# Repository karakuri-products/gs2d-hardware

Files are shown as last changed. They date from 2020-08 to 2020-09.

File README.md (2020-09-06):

# gs2d-hardware (gs2d Hardware Manual)

> gs2d ライブラリ・ハードウェアマニュアル

---

## gs2d 対応製品

gs2d 対応が確認できているシリアルサーボ・ドライバは表 1 のとおりです。

> 表 1 　対応製品一覧

| Manufacturer | Product Name |
| --- | --- |
| karakuri products Inc. | kr-gs2d001 |

karakuri products 社の kr-gs2d001 については ./kr-gs2d001 にまとめています。

---

## ドライバを自作する場合

### ハードウェア要件

gs2d に対応するシリアルサーボ・ドライバを開発する際、以下を満たしてください。

> 1. シリアル信号の送信/受信ライン間のループバックは回路的に無視すること。[↓](#ループバック処理)
> 2. 入力するシリアルおよび GPIO の I/O レベルが 5V 以下の場合は適宜、レベル変換を実装すること。[↓](#レベル変換)

### 設計例

#### ループバック処理

gs2d 対応シリアルバスの設計例を図 1 に示します。

入力するシリアルに対する送信許可信号（TxDEN）を 3 ステートバッファの制御信号に接続します。これにより信号の流れを制御し、送信コマンドの受信側へのループバックを回路的に無視することができます。

<div align="center">
    gs2d-hw fig.1
</div>

> 図 1 ループバック処理の一例

gs2d でサポートするシリアルサーボのバスの物理層は RS485、1 wire TTL Serial の 2 種に大別できます。各規格でのループバック処理の設計例は図 2、図 3 を参照ください。

<div align="center">
    gs2d-hw fig.2
</div>

> 図 2 RS485 方式での設計例

<div align="center">
    gs2d-hw fig.3
</div>

> 図 3 1 wire TTL Serial 方式での設計例

##### TxDEN について

FT232 などの USB シリアルドライバを利用する際は提供される TxDEN をそのまま活用できます。例えば、FT232 では出荷設定では CBUS2 端子に TxDEN 出力が割り当てられており、これを接続します（図 4）。

<div align="center">
    gs2d-hw fig.4
</div>

> 図 4 FT232 での接続例

Arduino、Teensy 等のマイコンからシリアルを入力する場合、TxDEN に適当な GPIO を接続します。この GPIO をシリアル送信/受診時に適切に制御することで、コマンドのループバックを遮断します。Arduino UNO での例を図 5 に示します。

接続した GPIO の制御は gs2d-cpp ライブラリの How to Use を確認ください。

<div align="center">
    gs2d-hw fig.5
</div>

> 図 5 Arduino UNO での接続例<br>
> (この例では、ディジタルピン 2 を TxDEN として活用、シリアルはハードウェア・シリアル)

#### レベル変換

シリアルサーボ側の信号ラインは一般的に +5V レベルが採用されており、 gs2d もこれに準じます。

上記の例（図 4 ～ 5）では、入力する RX、TX、TXDEN の I/O レベルが +5V であると仮定し、直接、シリアルバス・ドライバに接続していました。しかしそうでない場合（5V 未満の場合）は双方向レベル変換回路を接続し、I/O レベルの差異を吸収してください。

双方向レベル変換回路の具体的な設計例を図 6 に示します。この設計例は V<sub>IOREF</sub> = +5V の場合も対応します。

<div align="center">
    gs2d-hw fig.6
</div>

> 図 6 Nch MOS-FET を用いた双方向レベル変換回路の一例<br>
> R は 10kΩ 程度の抵抗、Q は Nch MOS-FET。V<sub>IOREF</sub> には低電圧 Lv. I/O 側の基準電圧を接続します。

図 6 を組込んだシリアルバス・ドライバの設計例を図 7 に示します。

<div align="center">
    gs2d-hw fig.７
</div>

> 図 7 レベル変換を組込んだシリアルバスドライバ回路の一例<br>
> (入力信号側の I/O レベルが +3.3V の場合)

より詳細な設計例は gs2d に対応済みのシリアルサーボドライバ kr-gs2d001 (karakuri products 製) の<a href="./kr-gs2d001/kr-gs2d001_schematic.pdf">回路図</a>を参照ください。

---

## ライセンス

gs2d は Apache License 2.0 とします。詳細は ./LICENSE を参照のこと。

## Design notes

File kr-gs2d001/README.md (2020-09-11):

# kr-gs2d001

> gs2d 対応 シリアルサーボ・ドライバ kr-gs2d001

<div align="center">
    gs2d-hw fig.1
</div>

---

## 概要

kr-gs2d001 は、gs2d ライブラリに対応したシリアルサーボ・ドライバです。

本製品と gs2d ライブラリにより、 2 種類の規格 ( RS485、1 wire TTL Serial ) のシリアルサーボを PC およびマイコンから簡単に制御することができます。

<div align="center">
    gs2d-hw fig.1
</div>

> 図 1 kr-gs2d001 外観 (左: 正面、右: 背面)

<div align="center">
    gs2d-hw fig.1
</div>

> 図 2 kr-gs2d001 ブロック図

---

### 対応シリアルサーボ

kr-gs2d001 でサポートするメーカ/規格は表 2 のとおりです。対応/動作確認が完了しているシリアルサーボの機種は<a href="https://docs.google.com/spreadsheets/d/15XlF4kySq219ICrvgJmQ_NEENOpA3_AKKTeR7gI3orM/edit?usp=sharing" target="_blank">こちら</a>で確認できます。

> 表 1 サポートするメーカ/規格

| Manufacturer | Series | Protocol |
| --- | --- | --- |
| ロボティズ (ROBOTIS Inc.) | Dynamixel X Series | Protocol 2.0 |
| 近藤科学 (Kondo Kagaku Co.,Ltd.) | B3M Serises <br> KRS Series | B3M protocol <br> ICS3.6 <br> ICS3.5 |
| 双葉電子工業 (FUTABA Corp.) | Command Type Servo | Command Type Protocol |

---

### 機械的仕様

> 表 2 機械的仕様

| 項目 | 仕様 |
| --- | --- |
| 基板外形 | 54.0 mm x 74.0 mm |

#### 3D モデルデータ

<a href="./3dmodel"> ./3dmodel </a>にて提供します。形式は表 3 のとおり。

> 表 3 提供モデルデータ形式一覧

| 拡張子 | 形式名 | 備考 |
| --- | --- | --- |
| .f3d | Autodesk FUSIN360 形式 | |
| .iam / .ipt | Autodesk Inventor 形式 | zip 形式で圧縮 |
| .iges | IGES 形式 | |
| .sat | SAT 形式 | |
| .step | IGES 形式 | |

#### コネクタ配置

> 表 4 コネクタ一覧

| 番号 | 種類 | 用途 |
| --- | --- | --- |
| CN1 ~ CN4 | JST-XH 4p | KONDO B3M (RS485) |
| CN5 ~ CN8 | JST-EH 4p | ROBOTIS Dynamixel X (RS485) |
| CN9 ~ CN12  | JST-EH 4p | FUTABA RS40x (RS485) |
| CN13 ~ CN16 | JST-ZH 3p | KONDO KRS33xx (1 wire TTL)  |
| CN17 ~ CN20 | QI(2550) 3p | 1 wire TTL Serial 共用 |
| CN21 ~ CN24 | JST-ADH 3p | FUTABA RS20x (1 wire TTL) |
| CN25 ~ CN28 | QI(2550) 6p,8p x2,10p | Arduino シールド |
| CN29 | USB typeC | USB2.1, PD 非対応 |
| CN30 | AMASS-XT60 2p | 電源コネクタ |

#### 部品配置

> 表 5 主要部品一覧

| 番号 | 用途 |
| --- | --- |
| SW1 | RS485 / 1 wire TTL Serial 切替え (図 3) |
| SW2 | USB シリアル入力 (USB typeC 経由) / Arduino シリアル入力 (もしくは外部シリアル入力) 切替え (図 4) |
| LED1 | USB シリアル TxLED |
| LED2 | USB シリアル RxLED |
| LED3 | 電源 LED |
| SJ1/SJ2 | Arduino ハードウェア/ソフトウェア シリアル切替え (図 5) |

<div align="center">
    sw1 fig.2
</div>

> 図 3 SW1 によるシリアル信号の通信規格の切替え<br>
> (a) RS485, (b) 1 wire TTL Serial

<div align="center">
    sw1 fig.3
</div>

> 図 4 SW2 による入力シリアル信号の切替え<br>
> (a) USB シリアル入力 (USB typeC 経由), (b) Arduino シリアル入力 (もしくは外部シリアル入力)

<div align="center">
    GettingStarted fig.1
</div>

> 図 5 Arduino ハードウェア/ソフトウェア シリアル切替え(SJ1/SJ2)

---

### 電気的仕様

> 表 6 電気的仕様一覧

| パラメータ | 値 |
| --- | --- |
| 電源電圧 | 5.0 ～ 24.0V |
| 対応入力 I/O レベル | 3.0 ～ 5.0V  |

#### 回路図

<a href="./kr-gs2d001_schematic.pdf"> kr-gs2d001_schematic.pdf </a> に示します。

---

## ライセンス

kr-gs2d001 は Apache License 2.0 とします。詳細は LICENSE 参照。

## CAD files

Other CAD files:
kr-gs2d001/3dmodel/kr-gs2d001.f3d

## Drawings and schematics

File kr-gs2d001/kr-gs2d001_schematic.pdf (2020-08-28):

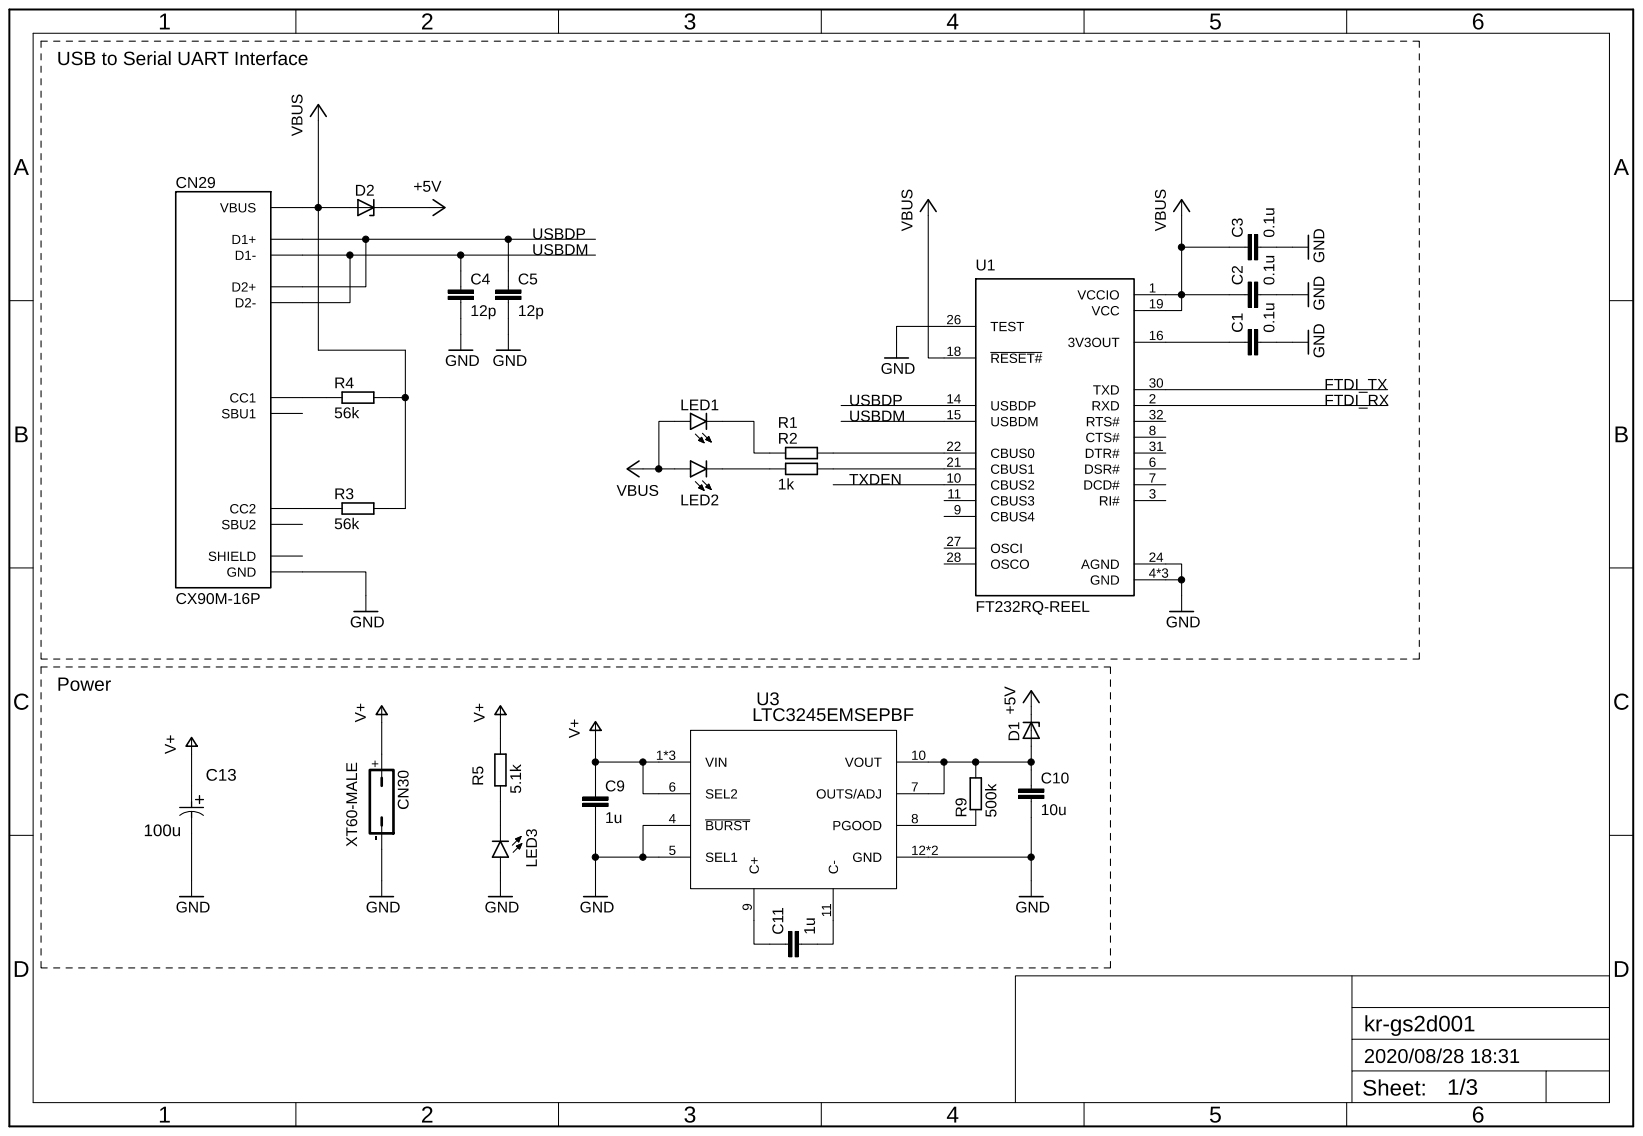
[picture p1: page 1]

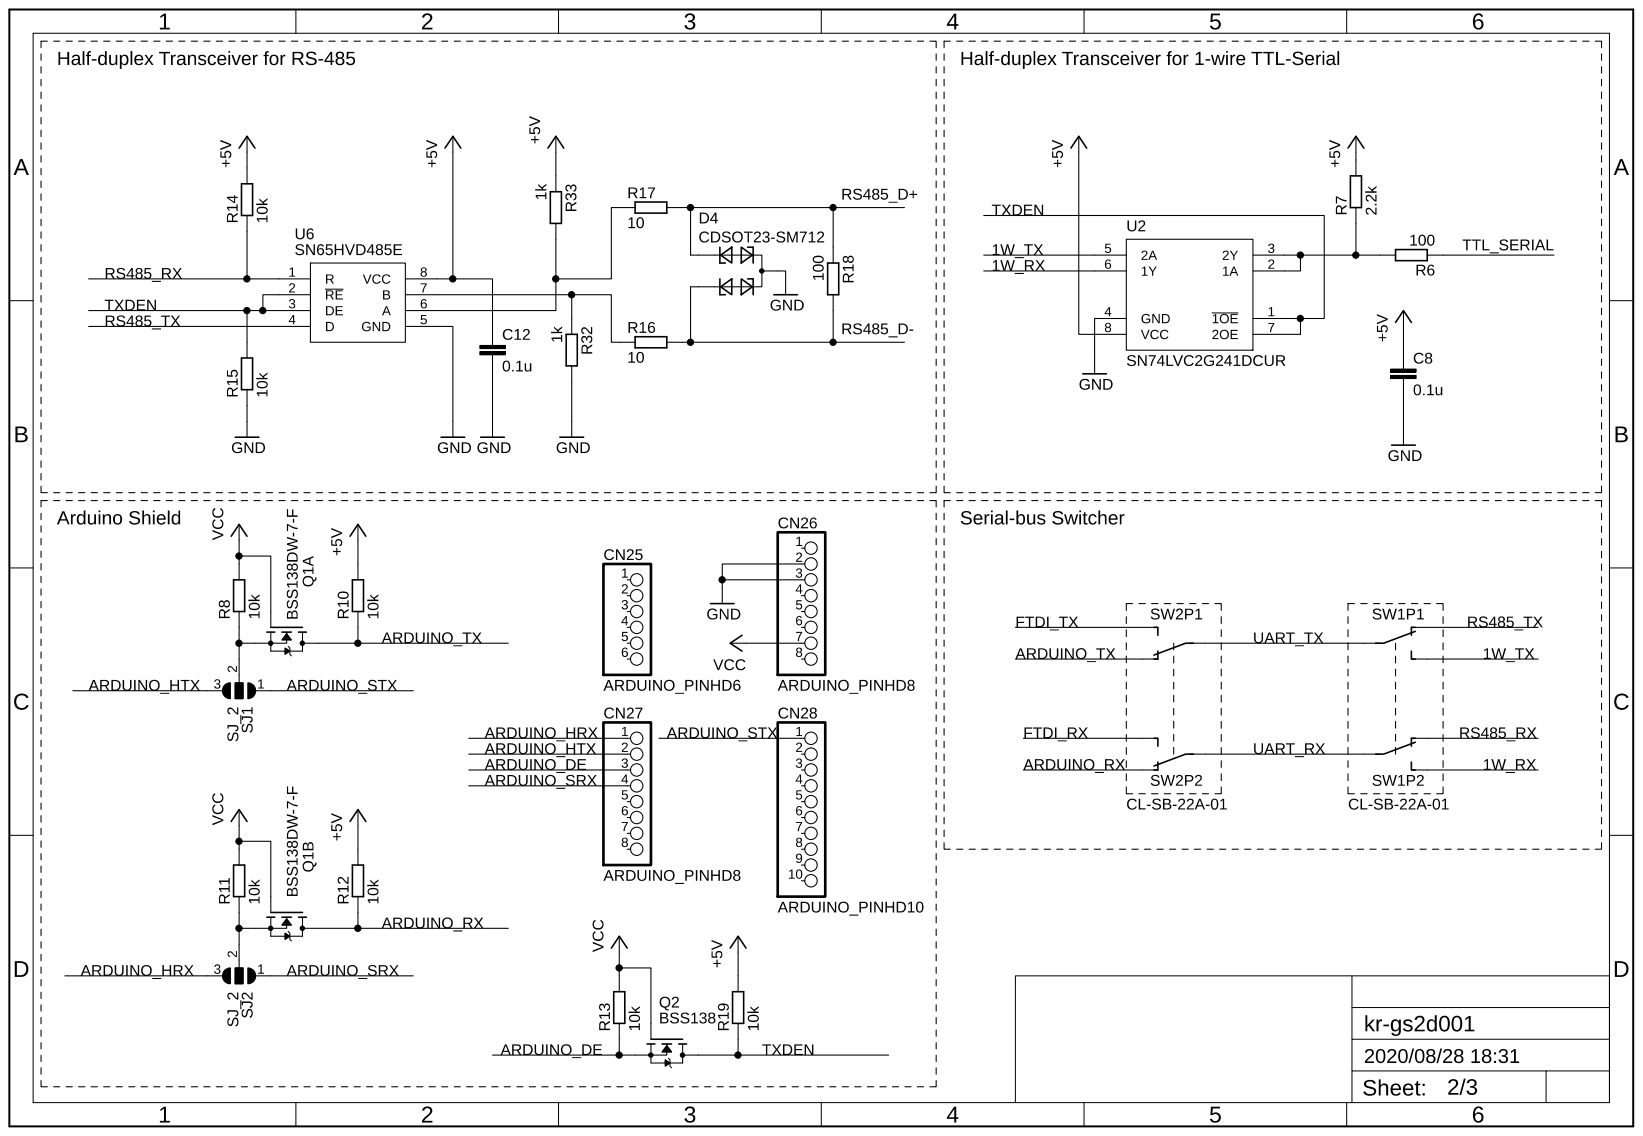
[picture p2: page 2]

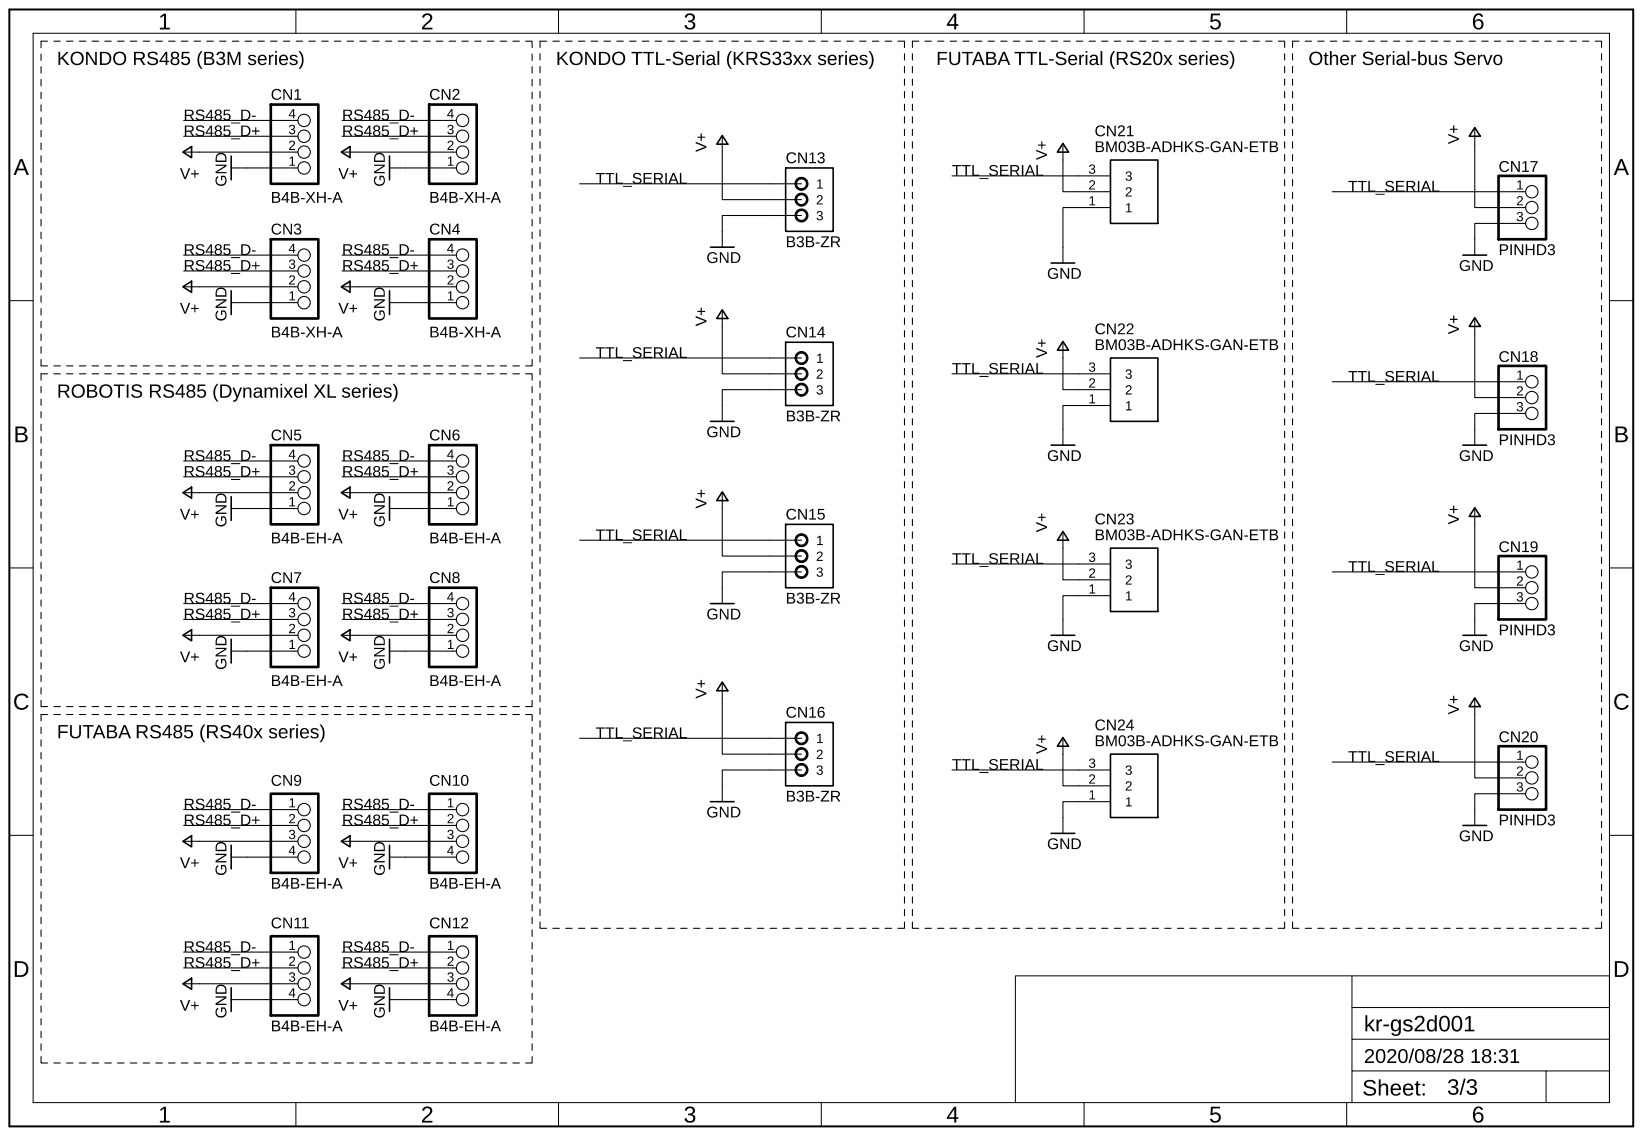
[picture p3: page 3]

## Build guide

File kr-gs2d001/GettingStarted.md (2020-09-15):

# Getting Started with kr-gs2d001

> kr-gs2d001 の使い方

---

## 目次

- **A: Arduino シールドとして使う** [↓](#gs2d-arduino)
  - (A-1) スイッチ (SW1, SW2) の設定 [↓](#A-1)
  - (A-2) ジャンパ (SJ1, SJ2) の設定 [↓](#A-2)
  - ピンヘッダの接続 [↓](#A-3)
- **B: マイコンに接続して使う** [↓](#gs2d-mcu)
  - (B-1) スイッチ (SW1, SW2) の設定 [↓](#B-1)
  - (B-2) ジャンパ (SJ1, SJ2) の設定 [↓](#B-1)
- **C: PC に接続して使う** [↓](#gs2d-pc)
  - (C-1) スイッチ (SW1, SW2) の設定 [↓](#C-1)

<!--
### シリアルサーボを動かしてみる

- C++ で動かしてみる
- Python で動かしてみる
- C# で動かしてみる
-->

---

### A: Arduino シールドとして使う [↑](#top)

kr-gs2d001 を Arduino シールドとして使う場合、以下の (A-1[↓](#A-1)), (A-2[↓](#A-2)) を設定し、Arduino に接続します [↓](#A-3)。

<div align="center">
    GettingStarted fig.a1
</div>

> 図 A1, Arduino シールドとして利用する場合の設定

#### (A-1) スイッチ (SW1, SW2) の設定 [↑](#top)

**SW2** を ○ 側に合わせ、シリアルサーボへの入力信号を **Arduino シリアル入力** 設定に切替えます(図 A2) 。

<div align="center">
    GettingStarted fig.a2
</div>

> 図 A2, SW2 の設定

制御するシリアルサーボの通信規格にあわせて **SW1** を切替え、設定します(図 3)。

<div align="center">
    GettingStarted fig.a3
</div>

> 図 A3, SW1 の設定

#### (A-2) ジャンパ (SJ1, SJ2) の設定 [↑](#top)

Arduino には、ハードウェアシリアルとソフトウェアシリアルの 2 系統のシリアル通信が用意されています。

利用するシリアルの種類に応じて **基板背面のジャンパ (SJ1, SJ2) をハンダでショートし、kr-gs2d001 に接続するシリアル信号を切替えてください**。

<div align="center">
    GettingStarted fig.A4
</div>

> 図 A4, 基板背面のジャンパ(SJ1, SJ2)

**SJ1, SJ2 を H 側にショート**させると **Arduino のハードウェアシリアルピン(RX:CN27-1, TX:CN27-2)を kr-gs2d001 に接続** します(図 A5)。

<div align="center">
    GettingStarted fig.A5
</div>

> 図 A5, ハードウェアシリアルを利用する場合

他方、**S 側にショート**させると **Arduino のソフトウェアシリアルピン(RX:CN27-4, TX:CN27-5)を kr-gs2d001 に接続** します(図 A6)。

<div align="center">
    GettingStarted fig.A6
</div>

> 図 A6, ソフトウェアシリアルを利用する場合

#### ピンヘッダの接続 [↑](#top)

CN25 ~ CN28 に 2.54mm ピンヘッダ（plug）をハンダ付けし、Arduino と接続します(図 A7)。

<div align="center">
    GettingStarted fig.2
</div>

> 図 A7, kr-gs2d001 と Arduino との接続 (図は Arduino UNO R3 との接続例)

<!--

#### 電源の供給

-->

---

### B: マイコンに接続して使う [↑](#top)

以下の (B-1[↓](#B-1)), (B-2[↓](#B-2)) を設定し、マイコンを接続します [↓](#B-3)。

<div align="center">
    GettingStarted fig.B1
</div>

> 図 B1, マイコンに接続して使う場合の設定

#### (B-1) スイッチ (SW1, SW2) の設定 [↑](#top)

**SW2** を ○ 側に合わせ、シリアルサーボへの入力信号を **外部シリアル入力** 設定に切替えます(図 B2) 。

<div align="center">
    GettingStarted fig.B2
</div>

> 図 B2, SW2 の設定

制御するシリアルサーボの通信規格にあわせて **SW1** を切替え、設定します(図 B3)。

<div align="center">
    GettingStarted fig.B3
</div>

> 図 B3, SW1 の設定

#### (B-2) ジャンパ (SJ1, SJ2) の設定 [↑](#top)

**基板背面のジャンパ (SJ1, SJ2)** を図 B4 中の **H 側もしくは S 側のいずれか一方にハンダでショート** し、外部シリアル信号を入力します。

<div align="center">
    GettingStarted fig.B4
</div>

> 図 B4, 基板背面のジャンパ(SJ1, SJ2)

**SJ1, SJ2 を H 側にショート**させると **kr-gs2d001 の RX に CN27-1 を、TX に CN27-2 を接続** します(図 B5)。

<div align="center">
    GettingStarted fig.B5
</div>

> 図 B5, H 側をショートさせた場合

他方、**S 側にショート**させると **kr-gs2d001 の RX に CN27-4 を、TX に CN27-5 を接続** します(図 B6)。

<div align="center">
    GettingStarted fig.B6
</div>

> 図 B6, S 側をショートさせた場合

---

### C: PC と接続して使う [↑](#top)

以下の (C-1[↓](#C-1)) を設定し、**kr-gs2d001 内蔵の USB シリアルと PC を接続**します [↓](#C-3)。

<div align="center">
    GettingStarted fig.2
</div>

> 図 C1, PC と接続して使う場合の設定

#### (C-1) スイッチ (SW1, SW2) の設定 [↑](#top)

**SW2** を ● 側に合わせ、シリアルサーボへの入力信号を **内蔵 USB シリアル入力** 設定に切替えます(図 B2) 。

<div align="center">
    GettingStarted fig.C2
</div>

> 図 C2, SW2 の設定

制御するシリアルサーボの通信規格にあわせて **SW1** を切替え、設定します(図 C3)。

<div align="center">
    GettingStarted fig.C3
</div>

> 図 C3, SW1 の設定

---

## ライセンス

kr-gs2d001 は Apache License 2.0 とします。詳細は LICENSE 参照。

[gs2d concept](https://github.com/karakuri-products/gs2d)

---

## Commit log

2020-08-27 ✎ add README.md
    ハードウェアマニュアルを追記。図を追加。
2020-08-27 ✎ add README.md
    図、その他を修正。
2020-08-27 ✎ add README.md
    図を追記。
2020-08-27 ✎ add README.md
    TxDENについて追記。
2020-08-27 ✎ Update README.md
    細かい修正。
2020-08-27 👍 add kr-gs2d001 content (3D model & schematic)
    kr-gs2d001 のモデルデータ回路図を追加
    [kr-gs2d001.f3d]
2020-08-27 ✎ update kr-gs2d001 contents
    kr-gs2d001 の回路図を修正。
2020-08-27 ✎ update kr-gs2d001_schamatic.pdf
    回路図修正。
2020-08-28 ✎ update README.md
2020-08-28 ✎ add kr-gs2d001/README.md
    kr-gs2d001 のドキュメントを追加。
2020-08-28 ✎ update kr-gs2d001/README.md
    kr-gs2d001 のドキュメント更新
2020-08-28 ✎ update kr-gs2d001/README.md
    kr-gs2d001 を修正。
2020-08-28 ✎ update kr-gs2d001/README.md / add kr-gs2d001/LICENSE
    追記およびライセンス追加。
2020-08-30 ✎ update kr-gs2d001/README.md
    kr-gs2d001 の説明の追記。
2020-09-06 ✎ update README.md, ./kr-gs2d001/README.md
    レベル変換回路の設計詳細についてを追記。その他、軽微な追記。
2020-09-06 ✎ update README.md
    図7 を微修正。
2020-09-06 ✎ update README.md
    typo 修正
2020-09-06 ✎ update README.md
    微修正。
2020-09-06 ✎ update README.md
    図6,図7を更新。
2020-09-06 ✎ update README.md
    図6、図7を修正。
2020-09-11 ✎ update kr-gs2d001/README.md
    ブロック図を追加。軽微な修正。
2020-09-11 ✎ add kr-gs2d001/GettingStarted.md
    取扱説明書を追加。
2020-09-11 ✎ update kr-gs2d001/GettingStarted.md
    図番が正しくないのを微修正。
2020-09-11 ✎ update kr-gs2d001/GettingStarted.md
    図の誤植を修正。
2020-09-11 ✎ update kr-gs2d001/README.md
    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
2020-09-14 ✎ update kr-gs2d001/GettingStarted.md
    Getting Started を追記。
2020-09-15 ✎ update kr-gs2d001/GettingStarted.md
    図を修正。追記。
2020-09-15 ✎ update kr-gs2d001/GettingStarted.md
    軽微な追記。
